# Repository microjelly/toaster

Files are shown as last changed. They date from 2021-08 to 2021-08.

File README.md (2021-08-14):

# toaster
A barebones toaster reflow board and software. For details please visit my [project log](https://microjelly.com/reflow-controller-replacement/)

## Software
### Build
This project currently is using a Docker based build system. 
\
\
*from a command line*
```bash
git clone https://github.com/microjelly/toaster.git
cd toaster/build
make sdcc/stm8s-ebake1.ihx
make sdcc/n76e003-ebake1.ihx
```
`stm8s-ebake1.ihx` and `n76e003-ebake1.ihx` will be found in the `build/bin` directory. 

### Flash STM8s
```bash
stm8flash -c stlinkv2 -p stm8s103?3 -w stm8s-ebake1.ihx
```

## Hardware
`hw/v1/bom/index.html` has component value and placement information.

### STM8s build
Reference | Value
-- | --
C5 | 1uF
R5 | DNP (Do Not Populate)
U1 | STM8S103F3P6

### N76E003 build
Reference | Value
-- | --
C5 | DNP (Do Not Populate)
R5 | 0 Ohm
U1 | N76E003AT20

### Programing/Debug Header
The header uses a 10pin card edge 2.54mm pitch connector.
```
Top with pads on the bottom right
 | 2| 4| 6| 8|10|

Bottom with pads on the bottom left
 | 1| 3| 5| 7| 9|
```

Pad | STM8s | N76E003
-- | -- | --
1 | 3v3 | 3v3
2 | 3v3 | 3v3
3 | GND | GND
4 | SWIM | ICPCK
5 | GND | GND
6 | GND | GND
7 | RX | RX
8 | NRST | RST
9 | TX | TX
10 | N/A | ICPDAT

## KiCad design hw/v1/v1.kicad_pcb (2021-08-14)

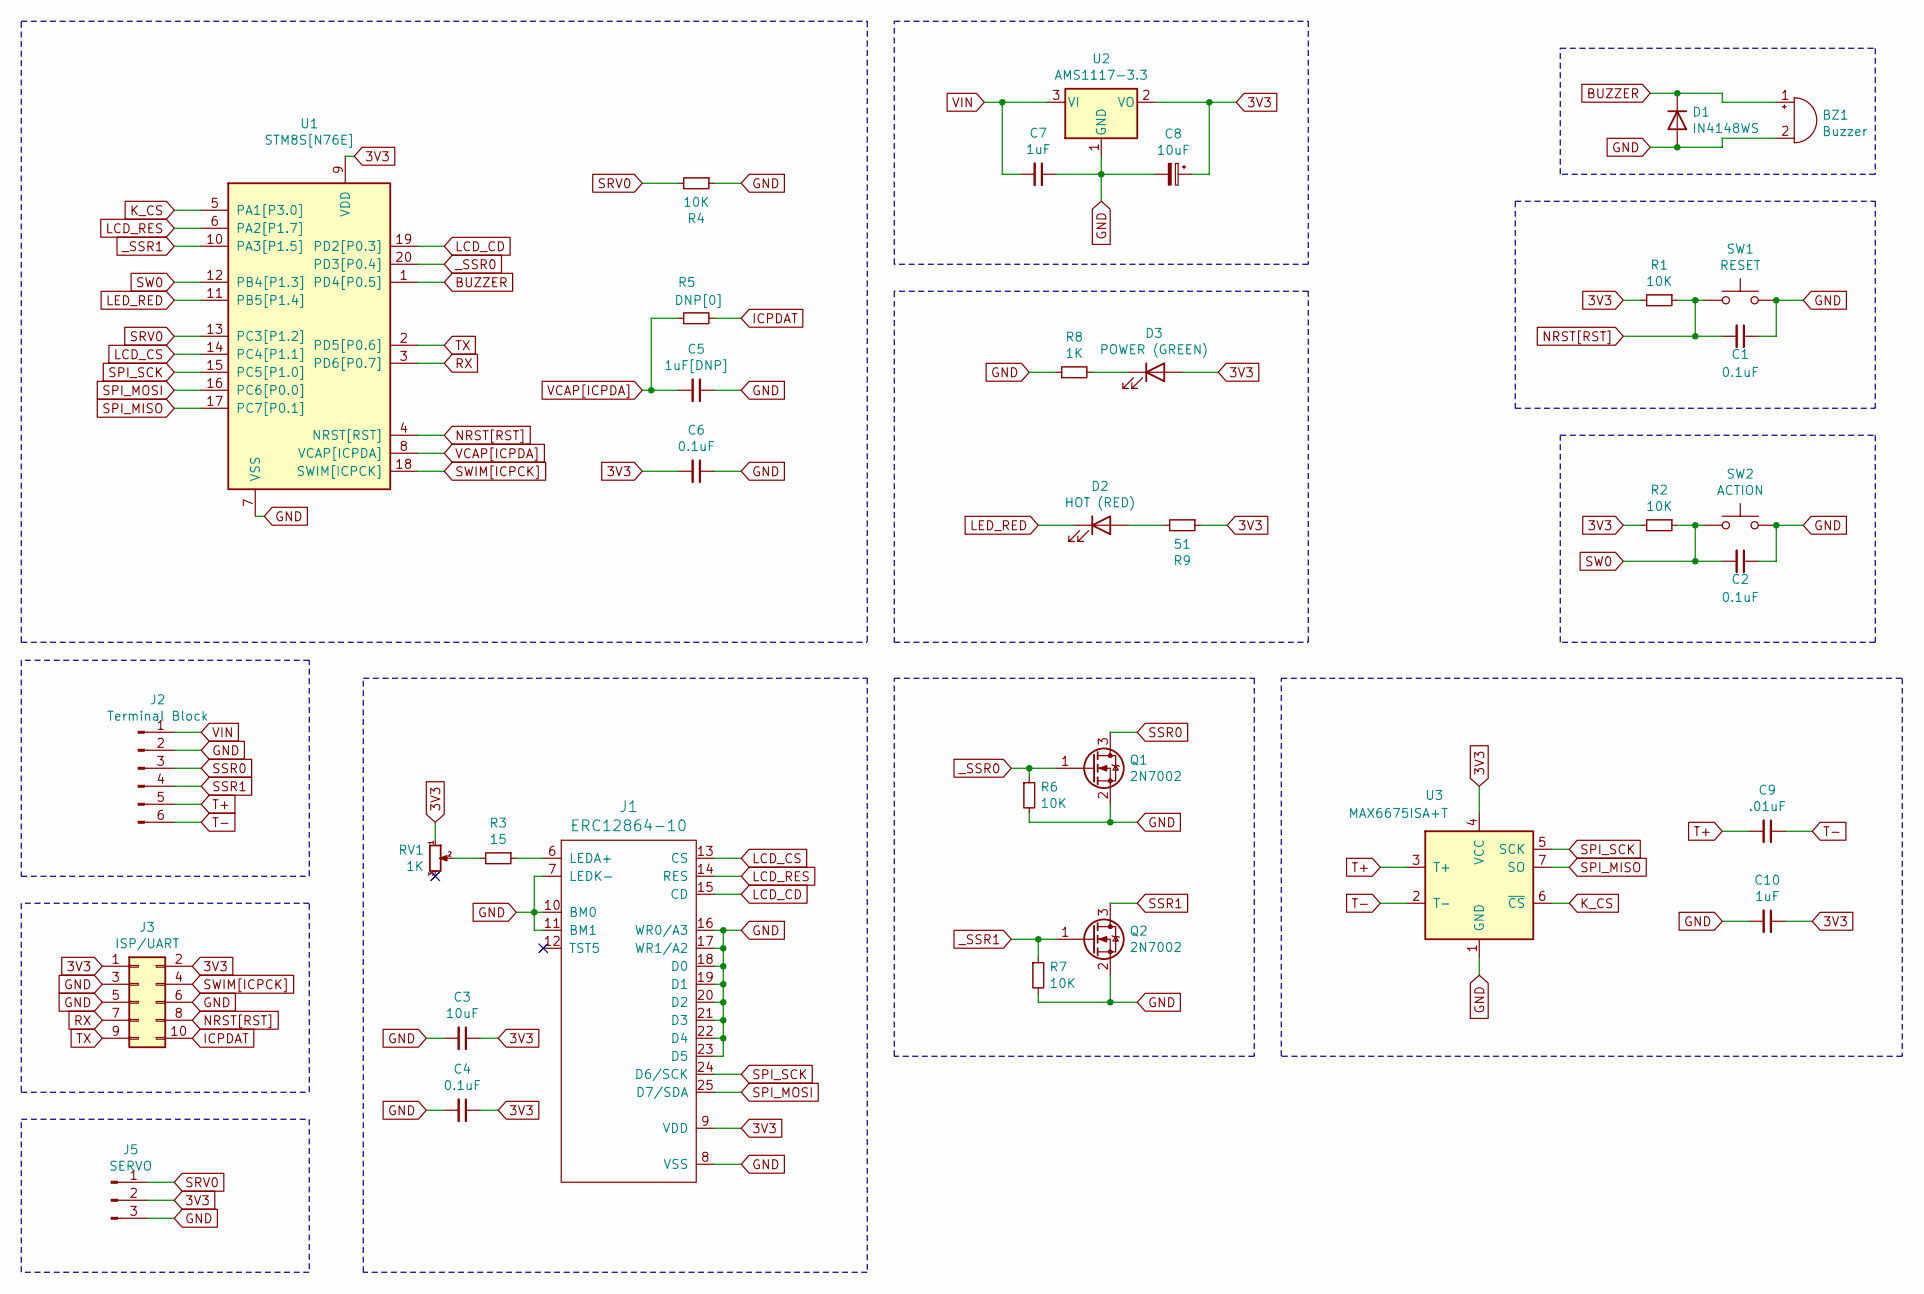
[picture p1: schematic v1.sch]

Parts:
BZ1: Buzzer; MLT-8530
C1, C2, C4, C6: 0.1uF; C_0805_2012Metric
C3: 10uF; C_0805_2012Metric
C5: 1uF[DNP]; C_0805_2012Metric
C7, C10: 1uF; C_0805_2012Metric
C8: 10uF; CP_EIA-3216-18_Kemet-A
C9: .01uF; C_0805_2012Metric
D1: IN4148WS; D_SOD-323
D2: HOT (RED); LED_0805_2012Metric
D3: POWER (GREEN); LED_0805_2012Metric
J1: ERC12864-10; ER-CON30HB-1
J2: Terminal Block; HT396V-3.96-6p
J3: ISP/UART; TRUDEAU_C2X5_SMD
J5: SERVO; PinHeader_1x03_P2.54mm_Vertical
Q1, Q2: 2N7002; SOT-23
R1, R2, R4, R6, R7: 10K; R_0805_2012Metric
R3: 15; R_0805_2012Metric
R5: DNP[0]; R_0805_2012Metric
R8: 1K; R_0805_2012Metric
R9: 51; R_0805_2012Metric
RV1: 1K; Potentiometer_Bourns_TC33X_Vertical
SW1: RESET; TS-1186D-C-A
SW2: ACTION; UK-B0229-G2.5-B-250
U1: STM8S[N76E]; TSSOP-20_4.4x6.5mm_P0.65mm
U2: AMS1117-3.3; SOT-223-3_TabPin2
U3: MAX6675ISA+T; SOIC-8_3.9x4.9mm_P1.27mm

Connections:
3V3: C3.1, C4.1, C6.2, C8.1, C10.1, D3.2 (A), J1.9 (VDD), J3.1, J3.2, J5.2, R1.2, R2.2, R9.1, RV1.1, U1.9 (VDD), U2.2 (VO), U3.4 (VCC)
BUZZER: BZ1.1 (-), D1.1 (K), U1.1 (PD4[P0.5])
GND: BZ1.2 (+), C1.1, C2.1, C3.2, C4.2, C5.1, C6.1, C7.1, C8.2, C10.2, D1.2 (A), J1.7 (LEDK-), J1.8 (VSS), J1.10 (BM0), J1.11 (BM1), J1.16 (WR0/A3), J1.17 (WR1/A2), J1.18 (D0), J1.19 (D1), J1.20 (D2), J1.21 (D3), J1.22 (D4), J1.23 (D5), J2.2, J3.3, J3.5, J3.6, J5.3, Q1.2 (S), Q2.2 (S), R4.1, R6.2, R7.2, R8.1, SW1.2, SW2.2, U1.7 (VSS), U2.1 (GND), U3.1 (GND)
ICPDAT: J3.10, R5.2
K_CS: U1.5 (PA1[P3.0]), U3.6 (~CS~)
LCD_CD: J1.15 (CD), U1.19 (PD2[P0.3])
LCD_CS: J1.13 (CS), U1.14 (PC4[P1.1])
LCD_RES: J1.14 (RES), U1.6 (PA2[P1.7])
LED_RED: D2.1 (K), U1.11 (PB5[P1.4])
NRST[RST]: C1.2, J3.8, R1.1, SW1.1, U1.4 (NRST[RST])
unnamed: D2.2 (A), R9.2
unnamed: D3.1 (K), R8.2
unnamed: J1.6 (LEDA+), R3.1
unnamed: R3.2, RV1.2
RX: J3.7, U1.3 (PD6[P0.7])
SPI_MISO: U1.17 (PC7[P0.1]), U3.7 (SO)
SPI_MOSI: J1.25 (D7/SDA), U1.16 (PC6[P0.0])
SPI_SCK: J1.24 (D6/SCK), U1.15 (PC5[P1.0]), U3.5 (SCK)
SRV0: J5.1, R4.2, U1.13 (PC3[P1.2])
SSR0: J2.3, Q1.3 (D)
SSR1: J2.4, Q2.3 (D)
SW0: C2.2, R2.1, SW2.1, U1.12 (PB4[P1.3])
SWIM[ICPCK]: J3.4, U1.18 (SWIM[ICPCK])
T+: C9.2, J2.5, U3.3 (T+)
T-: C9.1, J2.6, U3.2 (T-)
TX: J3.9, U1.2 (PD5[P0.6])
VCAP[ICPDA]: C5.2, R5.1, U1.8 (VCAP[ICPDA])
VIN: C7.2, J2.1, U2.3 (VI)
_SSR0: Q1.1 (G), R6.1, U1.20 (PD3[P0.4])
_SSR1: Q2.1 (G), R7.1, U1.10 (PA3[P1.5])

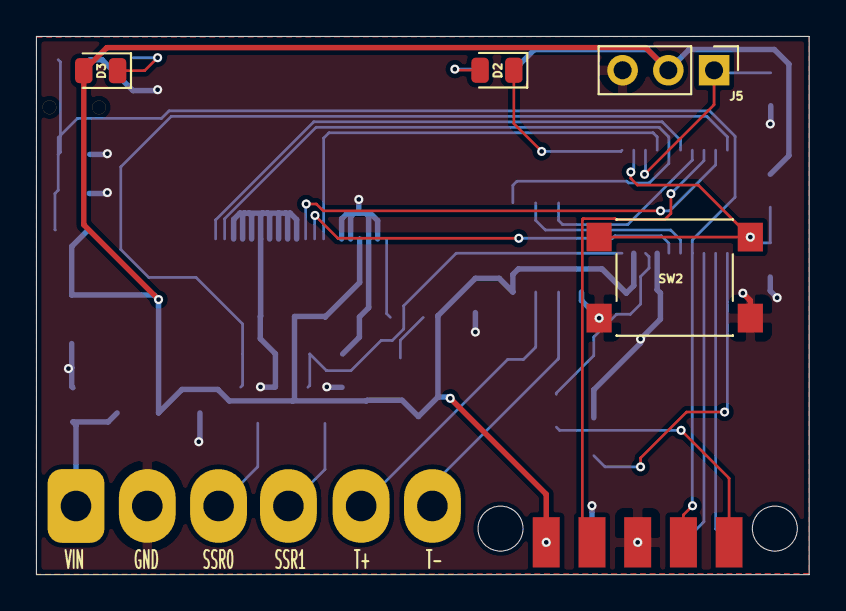
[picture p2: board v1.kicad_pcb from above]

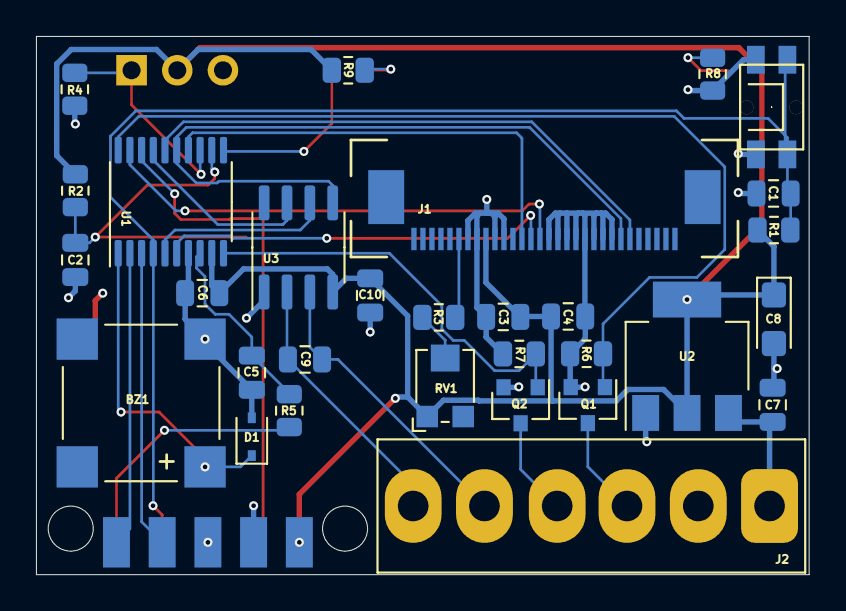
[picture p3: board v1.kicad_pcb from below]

Board: 2 copper layers, 42.9 x 29.9 mm, 35 parts (31 on the bottom side), 30 nets.

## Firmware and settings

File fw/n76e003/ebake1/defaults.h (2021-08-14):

#ifndef DEFAULTS_H
#define DEFAULTS_H

#define LED0 P14
#define SW0 P13

#define BUZZER_CLK (16000000 / 12)
#define BUZZER_FREQ (1200 * 2)
#define BUZZER_PERIOD (0xFFFF - ((BUZZER_CLK / BUZZER_FREQ) - 1))

#define PWM_CLK (16000000 / 8)
#define PWM_FREQ 240
#define PWM_PERIOD ((PWM_CLK / PWM_FREQ) - 1)
#define PWM_SLICE (PWM_PERIOD / 100)

#define SRV0_START 0

#define NUMBER_OF_OUTPUTS 2

#define DEFAULT_TEMP_COOL 45
#define DEFAULT_TEMP_HOT 50
#define DEFAULT_MAX_TEMP 280
#define DEFAULT_MAX_DEVIATION 20

#define DEFAULT_MAX_DUTY_TOP 75
#define DEFAULT_MAX_DUTY_BOTTOM 100

enum
{
    SM_GO_NULL = 0,
    SM_NULL,
    SM_GO_RUN,
    SM_RUN,
    SM_START_COOLING,
    SM_COOLING,
    SM_DONE,
    SM_DONE_Q
};

enum
{
    DISPLAY_CURRENT_SECOND = 0,
    DISPLAY_COUNTDOWN_TIMER,
    DISPLAY_PROFILE_TIMER,
};

enum
{
    ELEMENT_TOP = 0,
    ELEMENT_BOTTOM
};

enum
{
    PROFILE_FIRST = 0,
    PROFILE_MIDDLE,
    PROFILE_LAST,
};

#define PID_P 5
#define PID_I 2
#define PID_D 0

#define BIAS_MAX 100
#define BIAS_B 100
#define BIAS_T 95

const uint8_t profile[3][2] = {{150,40},{190,10},{245,12}};
#define PROFILE_LEN 3
#define PROFILE_TEMP 0
#define PROFILE_TIME 1
#define PROFILE_OVERSHOOT 10 // FIX the PID, don't do this!!
#define PROFILE_ADJUST 1

#endif /* DEFAULTS_H */

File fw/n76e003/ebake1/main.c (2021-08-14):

/*
 * N76E003-TOASTER
 *
 * LED
 *  LED0 -> P1.4 (RED; HOT)
 * SSR
 *  SSR0 -> P0.4;PWM3 > TOP
 *  SSR1 -> P1.5;PWM5 > BOTTOM
 * SERVO
 *  SRV0 -> P1.2;PWM0
 * SW
 *  SW0  -> P1.3
 * LCD
 *  CS   -> P1.1
 *  DC   -> P0.3
 *  RES  -> P1.7
 *  SCK  -> P1.0;SPCLK [spi]
 *  MOSI -> P0.0;MOSI  [spi]
 * MAX6675
 *  CS   -> P3.0
 *  SCK  -> P1.0;SPCLK [spi]
 *  MISO -> P0.1;MISO  [spi]
 * BEEP
 *  BEEP -> P0.5;T0
 * UART1
 *  TX   -> P0.6
 *  RX   -> P0.7
 */

#include <N76E003.h>
#include <SFR_Macro.h>
#include <Function_define.h>
#include <Common.h>
#include <Delay.h>
#include <stdbool.h>

#include <max6675.h>
#include <lcd.h>
#include "defaults.h"
#include "strings.h"
#include "pid.h"

/* Needed for printf */
int putchar(int c)
{
	while (!TI)
		;
	TI = 0;
	SBUF = c;
	return c;
}

void TIM0_ISR(void) __interrupt(1)
{
	clr_TF0;
	TL0 = LOBYTE(BUZZER_PERIOD);
	TH0 = HIBYTE(BUZZER_PERIOD);
}

volatile uint16_t tim2Value = 0;
void TIM2_ISR(void) __interrupt(5)
{
	clr_TF2;
	tim2Value++;
}

volatile uint8_t sw0Counter;
void PinInterrupt_ISR(void) __interrupt(7)
{
	if (PIF == 0x08)
	{
		PIF = 0;
		sw0Counter++;
	}
}

void setOutput(uint8_t value0, uint8_t value1)
{
	uint16_t pwm = PWM_SLICE * value0;
	if (pwm > 0)
	{
		PWM3H = HIBYTE(pwm);
		PWM3L = LOBYTE(pwm);
	}
	else
	{
		PWM3H = 0;
		PWM3L = 0;
	}

	pwm = PWM_SLICE * value1;
	if (pwm > 0)
	{
		set_SFRPAGE;
		PWM5H = HIBYTE(pwm);
		PWM5L = LOBYTE(pwm);
		clr_SFRPAGE;
	}
	else
	{
		set_SFRPAGE;
		PWM5H = 0;
		PWM5L = 0;
		clr_SFRPAGE;
	}
	while (LOAD == 1)
		;
	set_LOAD;
}

uint16_t setServo(uint8_t value0)
{
	uint16_t srv0 = (PWM_SLICE * 6) + (value0 * (PWM_SLICE/4));

	PWM0H = HIBYTE(srv0);
	PWM0L = LOBYTE(srv0);
	while (LOAD == 1)
		;
	set_LOAD;
	return srv0;
}

void setText(bool stdout, bool isTitle, struct LCD_SEGMENT *segment, uint8_t *format, ...)
{
    uint8_t *ptr = (uint8_t*)segment->buffer;
    lcd_clear_segment(segment);

    if (isTitle)
    {
        *ptr++;
        *ptr++;
    }

    va_list args;
    va_start(args, format);
    vsprintf(ptr, format, args);
    va_end(args);

    if (stdout)
    {
	   if (isTitle)
            *ptr++;
		printf_tiny("%s: '%s'\r\n", ((isTitle) ? " TITLE" : "STATUS"), ptr);
//        printf_tiny((isTitle) ? "TITLE: '" : "STATUS: '");
//        printf_tiny("%s", ptr);
//        printf_tiny("'\r\n");
    }
}

/*==========================================================================*/
void main(void)
{
	__xdata uint16_t previousTicks = 0xffff;
	__xdata uint16_t previousSecond = 0xffff;
	__xdata uint8_t servo0 = SRV0_START;
	__xdata uint8_t previousDutyCycle[NUMBER_OF_OUTPUTS] = {0, 0};
    __xdata uint8_t currentDutyCycle[NUMBER_OF_OUTPUTS] = {0, 0};

    __xdata bool isHeating = false;
    __xdata uint8_t stateMachine = SM_GO_NULL;
	__xdata uint8_t beeps = 2;
	__xdata bool beepOn = false;

    __xdata uint16_t profileTimer = 0;
    __xdata bool profileTimerRunning = false;
    __xdata uint8_t profileStep = 0;
    __xdata uint16_t desiredTemperature = 0;

    __xdata uint8_t currentPidDutyCycle = 0;
    __xdata uint8_t previousPidDutyCycle = 0xff;

    __xdata uint16_t countdownTimer = 0;
    __xdata uint8_t displayTime = DISPLAY_CURRENT_SECOND;
    __xdata uint8_t displayType = '+';

    __xdata pid_struct pid = {
        0, 0,   //dstate, istate
        10, 0,  //imax, imin  
        99, 0,  //max/min output limits
        PID_P, PID_I, PID_D //p, i, d gains
    };

	clr_EA;

	/* SW0 setup */
	sw0Counter = 0;
	P13_Input_Mode;
	clr_PIPS1;
	set_PIPS0;
	Enable_BIT3_FallEdge_Trig;
	set_EPI;

	/* LED setup */
	P14_Quasi_Mode;

	/* TIM0 setup / BUZZER */
	P05_PushPull_Mode;
	TIMER0_MODE1_ENABLE;
	TL0 = LOBYTE(BUZZER_PERIOD);
	TH0 = HIBYTE(BUZZER_PERIOD);
	set_ET0;
	set_T0OE;
	clr_TR0;

	/* TIM2 setup ~200ms */
	TIMER2_DIV_128;
	TIMER2_Auto_Reload_Delay_Mode;
	RCMP2L = LOBYTE(TIMER_DIV128_VALUE_250ms);
	RCMP2H = HIBYTE(TIMER_DIV128_VALUE_250ms);
	TL2 = 0;
	TH2 = 0;
	set_ET2;
	set_TR2;

	/* PWM setup */
	PWM_IMDEPENDENT_MODE;
	PWM_CENTER_TYPE;
	PWM_CLOCK_DIV_8;
	PWMPH = HIBYTE(PWM_PERIOD);
	PWMPL = LOBYTE(PWM_PERIOD);
	set_PWMRUN;

	/* SSR setup */
	P04_PushPull_Mode;
	P15_PushPull_Mode;
	PWM3_P04_OUTPUT_ENABLE;
	PWM5_P15_OUTPUT_ENABLE;

	/* SERVO setup */
	P12_PushPull_Mode;
	PWM0_P12_OUTPUT_ENABLE;

	/* MAX6675 setup */
	max6675_init();

	/* LCD setup */
	lcd_init(true);

	__xdata uint8_t lcdTitleBuffer[21];
	__xdata struct LCD_SEGMENT lcdTitle = {
		'#',					// clearChar
		lcdTitleBuffer,			// buffer
		sizeof(lcdTitleBuffer), // bufferDepth
		1,						// fontWidth
		1,						// fontHeight
		1,						// fontSpacing
		0,						// page0
		1,						// rows
	};
	lcd_clear_segment(&lcdTitle);
	__xdata uint8_t lcdTimeBuffer[11];
	__xdata struct LCD_SEGMENT lcdTime = {
		' ',				   // clearChar
		&lcdTimeBuffer,		   // buffer
		sizeof(lcdTimeBuffer), // bufferDepth
		2,					   // fontWidth
		2,					   // fontHeight
		1,					   // fontSpacing
		1,					   // page0
		1,					   // rows
	};
	lcd_clear_segment(&lcdTime);

	__xdata uint8_t lcdPowerTempBuffer[11];
	__xdata struct LCD_SEGMENT lcdPowerTemp = {
		' ',						// clearChar
		lcdPowerTempBuffer,			// buffer
		sizeof(lcdPowerTempBuffer), // bufferDepth
		2,							// fontWidth
		3,							// fontHeight
		1,							// fontSpacing
		3,							// page0
		1,							// rows
	};
	lcd_clear_segment(&lcdPowerTemp);

	__xdata uint8_t lcdStatusBuffer[21];
	__xdata struct LCD_SEGMENT lcdStatus = {
		'#',					 // clearChar
		lcdStatusBuffer,		 // buffer
		sizeof(lcdStatusBuffer), // bufferDepth
		1,						 // fontWidth
		2,						 // fontHeight
		1,						 // fontSpacing
		6,						 // page0
		1,						 // rows
	};
	lcd_clear_segment(&lcdStatus);

	/* UART0 setup */
	InitialUART0_Timer3(115200);
	TI = 1;

	set_EA;
	printf_tiny("\r\n\r\n");

	do
	{
		uint8_t currentSW0 = sw0Counter;
		sw0Counter = 0;
		uint16_t currentTicks = tim2Value;
		uint16_t currentTemperatureRaw = max6675_read();
		uint16_t currentTemperature = currentTemperatureRaw / 4;
		uint16_t currentTemperaturePoint = (currentTemperatureRaw - (currentTemperature * 4)) * 100;

		uint16_t currentSecond = (currentTicks / 4);
		bool isOneSecondInterval = false;

		if (previousTicks != currentTicks)
		{
			previousTicks = currentTicks;
			if (previousSecond != currentSecond)
			{
				previousSecond = currentSecond;
				isOneSecondInterval = true;
				if (profileTimerRunning)
                    profileTimer++;
			}
			if (beeps)
			{
				if ((currentTicks % 2) == 0)
				{
					set_TR0;
					beepOn = true;
				}
				else if (beepOn)
				{
					clr_TR0;
					beepOn = false;
					beeps--;
				}
			}
		}

        if (currentSW0 && stateMachine == SM_NULL)
        {
            stateMachine = SM_GO_RUN;
        }
        else if (currentSW0 && stateMachine == SM_DONE_Q)
        {
            stateMachine = SM_GO_NULL;
        }
        else if (currentSW0 && stateMachine > SM_NULL && stateMachine < SM_START_COOLING)
        {
            beeps += 2;
            stateMachine = SM_START_COOLING;
        }
        else if (currentTemperature > DEFAULT_TEMP_HOT && stateMachine < SM_GO_RUN)
        {
            setText(true, false, &lcdStatus, "%s %uC", ST_START_HOT, currentTemperature);
            beeps += 2;
            stateMachine = SM_START_COOLING;
        }

        if (currentTemperature == 0 && stateMachine > SM_GO_NULL)
        {
            setText(true, false, &lcdStatus, "%s", ST_THERMOCOUPLE_ERROR);
            beeps += 4;
            stateMachine = SM_START_COOLING;
        }
        else if (currentTemperature >= DEFAULT_TEMP_HOT)
        {
            LED0 = 0;
        }
        else if (currentTemperature < DEFAULT_TEMP_COOL)
        {
            LED0 = 1;
        }

        if (currentTemperature > DEFAULT_MAX_TEMP && stateMachine < SM_START_COOLING)
        {
            setText(true, false, &lcdStatus, "%s", ST_OVERTEMP);
            beeps += 4;
            stateMachine = SM_START_COOLING;
        }

        switch (stateMachine)
        {
        case SM_GO_NULL:
            setText(true, true, &lcdTitle, " %s %s", ST_TITLE, ST_VER);
            setText(true, false, &lcdStatus, "%s", ST_PRESS_BUTTON_TO_START);
            isHeating = false;
            profileStep = 0;
            displayTime = DISPLAY_CURRENT_SECOND;
            beeps = 0;
            clr_TR0;
            stateMachine = SM_NULL;

        case SM_NULL:
            break;

        case SM_GO_RUN:
            setText(true, true, &lcdTitle, " %s", ST_RUN);
            lcd_clear_segment(&lcdStatus);
            profileTimer = 0;
            profileTimerRunning = false;
            desiredTemperature = profile[profileStep][PROFILE_TEMP] + PROFILE_OVERSHOOT;
            displayTime = DISPLAY_PROFILE_TIMER;
            beeps += 1;
            isHeating = true;
            stateMachine = SM_RUN;

        case SM_RUN:
            if (!isOneSecondInterval)
                break;

            currentPidDutyCycle = update_pid(&pid, pid_guard(desiredTemperature, currentTemperature), currentTemperature);

            if ((profileTimerRunning == false) && (profile[profileStep][PROFILE_TEMP] - PROFILE_ADJUST <= currentTemperature))
            {
	            desiredTemperature = profile[profileStep][PROFILE_TEMP] + PROFILE_ADJUST;
                profileTimer = 0;
                profileTimerRunning = true;
            }
            if ((profileTimerRunning == true) && (profile[profileStep][PROFILE_TIME] <= profileTimer))
            {
                beeps += 1;
                if (++profileStep == PROFILE_LEN)
                    stateMachine = SM_START_COOLING;
                else
                    stateMachine = SM_GO_RUN;
            }
            break;

        case SM_START_COOLING:
            setText(true, true, &lcdTitle, " %s", ST_COOLING);
            isHeating = false;
            profileTimerRunning = true;
            profileTimer = 0;
            displayTime = DISPLAY_PROFILE_TIMER;
            beeps += 2;
            stateMachine = SM_COOLING;

        case SM_COOLING:
            if (isOneSecondInterval)
            {
                if (currentTemperature < DEFAULT_TEMP_HOT && profileTimer >= 1)
                {
                    isHeating = false;
                    stateMachine = SM_DONE;
                }
            }
            break;

        case SM_DONE:
            setText(true, true, &lcdTitle, " %s", ST_DONE);
            setText(true, false, &lcdStatus, "%s", ST_PRESS_TO_RESTART);
            isHeating = false;
            beeps += 6;
            stateMachine = SM_DONE_Q;

        case SM_DONE_Q:

            break;
        }

        if (isHeating)
        {
            if (previousPidDutyCycle != currentPidDutyCycle)
            {
                previousPidDutyCycle = currentPidDutyCycle;
                setOutput(currentPidDutyCycle, currentPidDutyCycle);
                currentDutyCycle[ELEMENT_TOP] = currentPidDutyCycle * BIAS_T / BIAS_MAX;
                currentDutyCycle[ELEMENT_BOTTOM] = currentPidDutyCycle * BIAS_B / BIAS_MAX;
            }
        }
        else
        {
            if (previousPidDutyCycle != 0)
            {
                setOutput(0, 0);
                previousDutyCycle[ELEMENT_TOP] = 0;
                previousDutyCycle[ELEMENT_BOTTOM] = 0;
            }
        }


		if (isOneSecondInterval)
		{
			lcd_clear_segment(&lcdTime);
            lcd_clear_segment(&lcdPowerTemp);

            if (stateMachine == SM_DONE_Q)
            { /*
                format_sprintf(oledTime->buffer, ((learningFailed) ? ST_FAILED : ((learningAborted) ? ST_ABORTED : ST_SUCCESS)));
                if (learningFailed)
                    format_sprintf(oledPowerTemp->buffer, "%s #%04u", ST_ERROR, learningFailed);
                else if (!learningAborted)
                    format_sprintf(oledPowerTemp->buffer, "%2u %3u %3u", learnedDutyCycle, learnedInertia, learnedInsulation);
             */
            }
            else
            {
                uint16_t dT = (displayTime == DISPLAY_CURRENT_SECOND) ? currentSecond : ((displayTime == DISPLAY_COUNTDOWN_TIMER) ? countdownTimer : profileTimer);
                uint16_t lm = (dT / 60);
                uint16_t tm = (lm % 60);
                uint8_t th = (lm / 60);
                uint8_t ts = (dT % 60);
				setText(false, false, &lcdTime,  "%c %02u:%02u:%02u", displayType, th, tm, ts);
				if (isHeating)
					setText(false, false, &lcdPowerTemp, "%02u:%02u %3u C", currentDutyCycle[ELEMENT_BOTTOM], currentDutyCycle[ELEMENT_TOP], currentTemperature);
				else
					setText(false, false, &lcdPowerTemp, "--:-- %3u C", currentTemperature);
				
            }

//			setText(true, false, &lcdTime, "? %02u:%02u:%02u", th, tm, ts);

			lcd_display_segment(&lcdTitle);
			lcd_display_segment(&lcdTime);
			lcd_display_segment(&lcdPowerTemp);
			lcd_display_segment(&lcdStatus);
		}

		set_IDL;
	} while (1);
}

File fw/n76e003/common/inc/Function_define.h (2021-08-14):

/*--------------------------------------------------------------------------
N76E003 Function_define.h V1.02

All function define inital setting file for Nuvoton N76E003
--------------------------------------------------------------------------*/

#include <stdio.h>

#define nop __asm__ ("NOP");


//16 --> 8 x 2
#define HIBYTE(v1)              ((UINT8)((v1)>>8))                      //v1 is UINT16
#define LOBYTE(v1)              ((UINT8)((v1)&0xFF))
//8 x 2 --> 16
#define MAKEWORD(v1,v2)         ((((UINT16)(v1))<<8)+(UINT16)(v2))      //v1,v2 is UINT8
//8 x 4 --> 32
#define MAKELONG(v1,v2,v3,v4)   (UINT32)((v1<<32)+(v2<<16)+(v3<<8)+v4)  //v1,v2,v3,v4 is UINT8
//32 --> 16 x 2
#define YBYTE1(v1)              ((UINT16)((v1)>>16))                    //v1 is UINT32
#define YBYTE0(v1)              ((UINT16)((v1)&0xFFFF))
//32 --> 8 x 4
#define TBYTE3(v1)              ((UINT8)((v1)>>24))                     //v1 is UINT32
#define TBYTE2(v1)              ((UINT8)((v1)>>16))
#define TBYTE1(v1)              ((UINT8)((v1)>>8)) 
#define TBYTE0(v1)              ((UINT8)((v1)&0xFF))

#define SET_BIT0        0x01
#define SET_BIT1        0x02
#define SET_BIT2        0x04
#define SET_BIT3        0x08
#define SET_BIT4        0x10
#define SET_BIT5        0x20
#define SET_BIT6        0x40
#define SET_BIT7        0x80
#define SET_BIT8        0x0100
#define SET_BIT9        0x0200
#define SET_BIT10       0x0400
#define SET_BIT11       0x0800
#define SET_BIT12       0x1000
#define SET_BIT13       0x2000
#define SET_BIT14       0x4000
#define SET_BIT15       0x8000

#define CLR_BIT0        0xFE
#define CLR_BIT1        0xFD
#define CLR_BIT2        0xFB
#define CLR_BIT3        0xF7
#define CLR_BIT4        0xEF
#define CLR_BIT5        0xDF
#define CLR_BIT6        0xBF
#define CLR_BIT7        0x7F

#define CLR_BIT8        0xFEFF
#define CLR_BIT9        0xFDFF
#define CLR_BIT10       0xFBFF
#define CLR_BIT11       0xF7FF
#define CLR_BIT12       0xEFFF
#define CLR_BIT13       0xDFFF
#define CLR_BIT14       0xBFFF
#define CLR_BIT15       0x7FFF

#define FAIL            1
#define PASS            0

/*****************************************************************************************
* For GPIO INIT setting 
*****************************************************************************************/
//------------------- Define Port as Quasi mode  -------------------
#define P00_Quasi_Mode				P0M1&=~SET_BIT0;P0M2&=~SET_BIT0
#define P01_Quasi_Mode				P0M1&=~SET_BIT1;P0M2&=~SET_BIT1
#define P02_Quasi_Mode				P0M1&=~SET_BIT2;P0M2&=~SET_BIT2
#define P03_Quasi_Mode				P0M1&=~SET_BIT3;P0M2&=~SET_BIT3
#define P04_Quasi_Mode				P0M1&=~SET_BIT4;P0M2&=~SET_BIT4
#define P05_Quasi_Mode				P0M1&=~SET_BIT5;P0M2&=~SET_BIT5
#define P06_Quasi_Mode				P0M1&=~SET_BIT6;P0M2&=~SET_BIT6
#define P07_Quasi_Mode				P0M1&=~SET_BIT7;P0M2&=~SET_BIT7
#define P10_Quasi_Mode				P1M1&=~SET_BIT0;P1M2&=~SET_BIT0
#define P11_Quasi_Mode				P1M1&=~SET_BIT1;P1M2&=~SET_BIT1
#define P12_Quasi_Mode				P1M1&=~SET_BIT2;P1M2&=~SET_BIT2
#define P13_Quasi_Mode				P1M1&=~SET_BIT3;P1M2&=~SET_BIT3
#define P14_Quasi_Mode				P1M1&=~SET_BIT4;P1M2&=~SET_BIT4
#define P15_Quasi_Mode				P1M1&=~SET_BIT5;P1M2&=~SET_BIT5
#define P16_Quasi_Mode				P1M1&=~SET_BIT6;P1M2&=~SET_BIT6
#define P17_Quasi_Mode				P1M1&=~SET_BIT7;P1M2&=~SET_BIT7
#define P30_Quasi_Mode				P3M1&=~SET_BIT0;P3M2&=~SET_BIT0
//------------------- Define Port as Push Pull mode -------------------
#define P00_PushPull_Mode			P0M1&=~SET_BIT0;P0M2|=SET_BIT0
#define P01_PushPull_Mode			P0M1&=~SET_BIT1;P0M2|=SET_BIT1
#define P02_PushPull_Mode			P0M1&=~SET_BIT2;P0M2|=SET_BIT2
#define P03_PushPull_Mode			P0M1&=~SET_BIT3;P0M2|=SET_BIT3
#define P04_PushPull_Mode			P0M1&=~SET_BIT4;P0M2|=SET_BIT4
#define P05_PushPull_Mode			P0M1&=~SET_BIT5;P0M2|=SET_BIT5
#define P06_PushPull_Mode			P0M1&=~SET_BIT6;P0M2|=SET_BIT6
#define P07_PushPull_Mode			P0M1&=~SET_BIT7;P0M2|=SET_BIT7
#define P10_PushPull_Mode			P1M1&=~SET_BIT0;P1M2|=SET_BIT0
#define P11_PushPull_Mode			P1M1&=~SET_BIT1;P1M2|=SET_BIT1
#define P12_PushPull_Mode			P1M1&=~SET_BIT2;P1M2|=SET_BIT2
#define P13_PushPull_Mode			P1M1&=~SET_BIT3;P1M2|=SET_BIT3
#define P14_PushPull_Mode			P1M1&=~SET_BIT4;P1M2|=SET_BIT4
#define P15_PushPull_Mode			P1M1&=~SET_BIT5;P1M2|=SET_BIT5
#define P16_PushPull_Mode			P1M1&=~SET_BIT6;P1M2|=SET_BIT6
#define P17_PushPull_Mode			P1M1&=~SET_BIT7;P1M2|=SET_BIT7
#define P30_PushPull_Mode			P3M1&=~SET_BIT0;P3M2|=SET_BIT0
#define GPIO1_PushPull_Mode		P1M1&=~SET_BIT0;P1M2|=SET_BIT0
//------------------- Define Port as Input Only mode -------------------
#define P00_Input_Mode				P0M1|=SET_BIT0;P0M2&=~SET_BIT0
#define P01_Input_Mode				P0M1|=SET_BIT1;P0M2&=~SET_BIT1
#define P02_Input_Mode				P0M1|=SET_BIT2;P0M2&=~SET_BIT2
#define P03_Input_Mode				P0M1|=SET_BIT3;P0M2&=~SET_BIT3
#define P04_Input_Mode				P0M1|=SET_BIT4;P0M2&=~SET_BIT4
#define P05_Input_Mode				P0M1|=SET_BIT5;P0M2&=~SET_BIT5
#define P06_Input_Mode				P0M1|=SET_BIT6;P0M2&=~SET_BIT6
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

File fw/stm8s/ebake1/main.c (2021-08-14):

/*
 * STM8S-TOASTER
 *
 * LED
 *  LED0 -> PB5 (RED; HOT)
 * SSR
 *  SSR0 -> PD3 [tim2-ch2] > TOP
 *  SSR1 -> PA3 [tim2-ch3] > BOTTOM
 * SW
 *  SW0  -> PB4
 * OLED
 *  CS   -> PC4
 *  DC   -> PD2
 *  RES  -> PC3
 *  SCK  -> PC5 [spi]
 *  MOSI -> PC6 [spi]
 * MAX6675
 *  CS   -> PA1
 *  SCK  -> PC5 [spi]
 *  MISO -> PC7 [spi]
 * BEEP
 *  BEEP -> PD4
 * UART1
 *  TX   -> PD5
 *  RX   -> PD6
 */

#include <stdint.h>
#include <stdbool.h>
#include <stm8s.h>
#include <clock.h>
#include <format.h>
#include <uart_stdout.h>
#include <uart.h>
#include <lcd12864.h>
#include <max6675.h>
#include <beep.h>

#include "defaults.h"
#include "strings.h"
#include "pid.h"

void setOutput(uint8_t value0, uint8_t value1)
{
    uint16_t ccr = ((PWM_CLK / PWM_FREQ) * value0) / 100;
    if (ccr > 0)
    {
        TIM2_CCR2H = ccr >> 8; // Start off
        TIM2_CCR2L = ccr & 0x00FF;
    }
    else
    {
        TIM2_CCR2H = 0;
        TIM2_CCR2L = 0;
    }
    ccr = ((PWM_CLK / PWM_FREQ) * value1) / 100;
    if (ccr > 0)
    {
        TIM2_CCR3H = ccr >> 8; // Start off
        TIM2_CCR3L = ccr & 0x00FF;
    }
    else
    {
        TIM2_CCR3H = 0;
        TIM2_CCR3L = 0;
    }
}

void setText(bool stdout, bool isTitle, struct LCD12864_SEGMENT *segment, uint8_t *format, ...)
{
    uint8_t *ptr = segment->buffer;
    lcd12864_clear_segment(segment);

    if (isTitle)
    {
        *ptr++;
        *ptr++;
    }

    va_list args;
    va_start(args, format);
    format_vsprintf(ptr, format, args);
    va_end(args);

    if (stdout)
    {
        if (isTitle)
            *ptr++;
        putstring((isTitle) ? "TITLE: '" : "STATUS: '");
        putstring(ptr);
        putstring("'\r\n");
    }
}

/* TIM1 Update/Overflow interrupt handling routine */
static volatile uint16_t tim1Value;
void TIM1_update(void) __interrupt(TIM1_OVR_UIF_IRQ)
{
    tim1Value++;
    TIM1_SR1 &= ~TIM_SR1_UIF;
}

static volatile uint8_t extiButton;
ISR(gpio_isr, EXTI_PORTB_vector)
{
    extiButton++;
}

int main(void)
{
    volatile uint16_t previousTicks = 0xffff;
    volatile uint16_t previousSecond = 0xffff;
    volatile uint8_t previousDutyCycle[NUMBER_OF_OUTPUTS] = {0, 0};
    volatile uint8_t currentDutyCycle[NUMBER_OF_OUTPUTS] = {0, 0};

    volatile bool isHeating = false;
    volatile uint8_t stateMachine = SM_GO_NULL;
    volatile uint8_t beeps = 2;
    volatile bool beepOn = false;

    volatile uint16_t profileTimer = 0;
    volatile bool profileTimerRunning = false;
    volatile uint8_t profileStep = 0;
    volatile uint16_t desiredTemperature = 0;

    volatile uint8_t currentPidDutyCycle = 0;
    volatile uint8_t previousPidDutyCycle = 0xff;

    volatile uint16_t countdownTimer = 0;
    volatile uint8_t displayTime = DISPLAY_CURRENT_SECOND;
    volatile uint8_t displayType = '+';

    volatile pid_struct pid = {
        0, 0,   //dstate, istate
        10, 0,  //imax, imin
        99, 0,  //max/min output limits
        2, 3, 0 //1, 1, 0 //p, i, d gains
    };

    sim();
    clock_init();
    uart_init();
    max6675_init();
    beep_init();

    /* LED setup */
    PORT(LED0_PORT, DDR) |= LED0_PIN;
    PORT(LED0_PORT, CR1) |= LED0_PIN;

    /* TIM1 setup ~250ms */
    tim1Value = 0;
    TIM1_PSCRH = 0x10;
    TIM1_PSCRL = 0x00;
    TIM1_ARRH = 0x03;
    TIM1_ARRL = 0xd0;
    TIM1_IER |= TIM_IER_UIE;
    TIM1_CR1 |= TIM_CR1_CEN;

    /* TIM2/PWM setup */
    TIM2_PSCR = PWM_PSCR;
    TIM2_ARRH = PWM_ARR >> 8;
    TIM2_ARRL = PWM_ARR & 0x00FF;
    PORT(SSR0_PORT, DDR) |= SSR0_PIN;
    PORT(SSR0_PORT, CR1) |= SSR0_PIN;
    TIM2_CCER1 |= TIM2_CCER1_CC2E;
    TIM2_CCMR2 |= (TIM2_CCMR2_OC2M1 | TIM2_CCMR2_OC2M2);
    TIM2_CCMR2 &= ~TIM2_CCMR2_OC2M0;
    TIM2_CCR2H = 0;
    TIM2_CCR2L = 0;
    PORT(SSR1_PORT, DDR) |= SSR1_PIN;
    PORT(SSR1_PORT, CR1) |= SSR1_PIN;
    TIM2_CCER2 |= TIM2_CCER2_CC3E;
    TIM2_CCMR3 |= (TIM2_CCMR2_OC2M1 | TIM2_CCMR2_OC2M2);
    TIM2_CCMR3 &= ~TIM2_CCMR2_OC2M0;
    TIM2_CCR3H = 0;
    TIM2_CCR3L = 0;
    TIM2_CR1 |= TIM2_CR1_CEN;

    /* EXTI1 BUTTON setup */
    extiButton = 0;
    PB_CR2 = PIN4;
    EXTI_CR1 &= ~0x0C;
    EXTI_CR1 |= 0x08;

    rim();
    putstring("\r\n\r\n");

    if (!lcd12864_init(true))
    {
        putstring("LCD FAIL\r\n");
        while (1)
            ;
    }
    struct LCD12864_SEGMENT *lcdTitle = lcd12864_new_segment(0, 1, 1, 1, 1, '#');
    struct LCD12864_SEGMENT *lcdTime = lcd12864_new_segment(1, 2, 2, 1, 1, ' ');
    struct LCD12864_SEGMENT *lcdPowerTemp = lcd12864_new_segment(3, 2, 3, 1, 1, ' ');
    struct LCD12864_SEGMENT *lcdStatus = lcd12864_new_segment(6, 1, 2, 1, 1, '#');

    do
    {
        volatile uint16_t currentTicks = tim1Value;
        volatile uint8_t currentButton = extiButton;
        volatile uint16_t currentTemperature = (max6675_read() / 4);
        extiButton = 0;
        volatile uint16_t currentSecond = (currentTicks / 4);
        volatile bool isOneSecondInterval = false;

        if (previousTicks != currentTicks)
        {
            previousTicks = currentTicks;
            if (previousSecond != currentSecond)
            {
                previousSecond = currentSecond;
                isOneSecondInterval = true;
                if (profileTimerRunning)
                    profileTimer++;
            }
            if (beeps)
            {
                if ((currentTicks % 2) == 0)
                {
                    beep_on();
                    beepOn = true;
                }
                else if (beepOn)
                {
                    beep_off();
                    beepOn = false;
                    beeps--;
                }
            }
        }

        if (currentButton && stateMachine == SM_NULL)
        {
            stateMachine = SM_GO_RUN;
        }
        else if (currentButton && stateMachine == SM_DONE_Q)
        {
            stateMachine = SM_GO_NULL;
        }
        else if (currentButton && stateMachine > SM_NULL && stateMachine < SM_START_COOLING)
        {
            beeps += 2;
            stateMachine = SM_START_COOLING;
        }
        else if (currentTemperature > DEFAULT_TEMP_HOT && stateMachine < SM_GO_RUN)
        {
            setText(true, false, lcdStatus, "%s %uC", ST_START_HOT, currentTemperature);
            beeps += 2;
            stateMachine = SM_START_COOLING;
        }

        if (currentTemperature == 0 && stateMachine > SM_GO_NULL)
        {
            setText(true, false, lcdStatus, "%s", ST_THERMOCOUPLE_ERROR);
            beeps += 4;
            stateMachine = SM_START_COOLING;
        }
        else if (currentTemperature >= DEFAULT_TEMP_HOT)
        {
            PORT(LED0_PORT, ODR) &= ~LED0_PIN;
        }
        else if (currentTemperature < DEFAULT_TEMP_COOL)
        {
            PORT(LED0_PORT, ODR) |= LED0_PIN;
        }
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

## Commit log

2021-01-21 rm hw; plan to add kicad files after next rev
    [toaster-B_Paste.gbr, toaster-F_Paste.gbr]
2021-08-14 v1 hw/fw
    [v1-B_Cu.gbr, v1-B_Mask.gbr, v1-B_Paste.gbr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]
